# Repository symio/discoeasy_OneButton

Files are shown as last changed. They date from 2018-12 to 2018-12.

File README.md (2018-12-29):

# discoeasy_OneButton
Modifications pour Marlin_1.1.0RC6 par Dagoma afin d'activer la prise en compte d'un bouton pause/marche sur l'entrée Z-

Ce mod permet également de conserver certains réglages en vue de futures mises à jour.

vous pouvez configurer : 

 - Le nom de votre imprimante 
 - Le nivelage à 9 points de palpage (non proposé par Dagoma) 
 - Le bouton pause sans dépendance de l'extrudeur+ 
 - L'inversion des ports des extrudeurs
 - Les trapézoïdales sans pack expert 
 - Les pid x,y,z et E 

# Disclaimer :
Je ne suis pas associé ni employé par la société Dagoma.
Ce que je vous propose ici fonctionne sur ma DiscoEasy 200 équipée d'un écran et sur la base du firmware officiel Dagoma à partir du date du 2018/04/04-14h27 
choisit sur https://dist.dagoma.fr/ avec pour options : "avec écran" et "sans filamentRunout".

Ce mod est compatible avec le pack expert ou un pack expert maison ainsi qu'avec l'extrudeur +.

L'objectif et d'activer le mode de changement rapide de filament sur l'action d'un bouton comme Dagoma le propose dans son AddOn numéro2 "extrudeur+" sans l'extrudeur amélioré par Dagoma.
Pour fonctionner vous devez connecter un bouton poussoir sur le port "z-" de la carte MKS base.

L'objectif secondaire est de conserver vos personnalisation du firmware en cas de mise à jour.

N'hésitez pas à me contacter pour demander des ajouts de config.

C'est ce mod que j'utilise sur mon imprimante et pour moi cela fonctionne. 
Je suis prêt à vous aider mais n'endosserais aucune responsabilité quand à l'usage de ce mod.
Je considère que je m'adresse à des adultes responsables prêt à prendre à leurs charge leurs responsabilités.

Vous utilisez ce hack à vos risques et périls.

# configuration :

Lisez ce [guide](https://github.com/symio/discoeasy_OneButton/blob/master/config.md) pour configurer vos options.

Tous les détails de configuration et explications s'y trouvent.

# installation :

 - Copiez les fichiers dans le répertoire Marlin ou vous avez extrait les derniers fichiers source fournit par Dagoma (cf https://dist.dagoma.fr/)
Pour installer ce hack vous avez 2 possibilités :
1°) appliquer des patchs
 - Appliquez les patchs de code source fournit sur ce dépôt :
 -- Configuration.h.patch
 -- pins.h.patch
 -- ultralcd.cpp.patch
 
 2°) Modifiez les fichiers de code sources suivants :
- Configuration.h :
 Ligne 41  ajoutez :

```cpp
 #define MODED_EASY_BOARD
```
- Fichier pins.h à la fin du fichier ajoutez :

```cpp
#if defined(MODED_EASY_BOARD) && !defined(MODED_EASY_H)
  #include "moded_easy.h"
#endif
```
- Fichier ultralcd.cpp remplacez la ligne 762 telle que :

```cpp
    //#if ENABLED(SUMMON_PRINT_PAUSE)
    #if ENABLED(SUMMON_PRINT_PAUSE) && ENABLED(FILAMENT_RUNOUT_SENSOR)
```
# Appliquer les fichiers de patchs :
1°) sous Linux :
- Ouvrez un terminal et naviguer jusqu'à vos sources
`$ cd ~/Documents/Marlin/`
- Vérifiez la présence des patchs :
```
$ ll *.patch
 Configuration.h.patch
 pins.h.patch
 ultralcd.cpp.patch
```
- Patchez chaque fichier individuellement :
`$ patch Configuration.h < Configuration.h.patch`
`$ patch pins.h < pins.h.patch`
`$ patch ultralcd.cpp < ultralcd.cpp.patch`

2°) sous Windows :
- Suivez cette documentation : https://docs.moodle.org/dev/How_to_apply_a_patch
- placez votre terminal au répertoire sources fourni par Dagoma (et dans lequel vous avez copié les fichiers de patch et la configuration)
- Patchez chaque fichier individuellement :
`c:\bin\patch.exe Configuration.h < Configuration.h.patch`
`c:\bin\patch.exe pins.h < pins.h.patch`
`c:\bin\patch.exe ultralcd.cpp < ultralcd.cpp.patch`

# Options de configuration :
Dans le fichier moded_easy.h :
- Les lignes 3 et 5 permettent de choisir :
-- ligne 3 Auto nivellage à 9 points avec bonne couverture de la surface du plateau
-- ligne 5 Mod one button
- commentez ou décommentez les lignes qui vous interressent
-- ex: activer le mod : (ligne 5)
`  #define ONE_BUTTON_MOD	 // active ou désactive le mod one button`
-- ex: désactiver le mod : (ligne 5)
`  //#define ONE_BUTTON_MOD	 // active ou désactive le mod one button`

# compiler et flasher l'imprimante

En suivant les tutos disponibles sur internet (https://www.lesimprimantes3d.fr/forum/topic/6228-tuto-flasher-firmware-discoeasy/) compilez et téléverser votre firmaware modifié avec Arduino dans votre imprimante.

# conclusion :
Il ne vous reste qu'à brancher un bouton poussoir sur le endstop Z- comme sur la vidéo de montage de l'extrudeur+ sur le site de Dagoma.

Enjoy et n'hésitez pas à envoyer des pull requests ou ouvrir des tickets si vous avez des soucis.

Photos et vidéo du montage ici : https://www.lesimprimantes3d.fr/forum/topic/14344-mod-bouton-pausechange-fil-pour-discoeasy200/

Le stl de face avant modifiée est là : https://www.tinkercad.com/things/0Ngym5hLYUM-discoeasy200modonebutton

Merci au Dagonautes sur le forum et sur Facebook vous êtes géniaux les mecs (et les filles) (sauf un ou deux dont moi bien sur) ...

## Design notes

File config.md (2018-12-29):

# Loamok ModedEasy200 configuration

Allez hop nouvelle version vous pouvez configurer : 

 - Le nom de votre imprimante 
 - Le nivelage à 9 points de palpage (non proposé par Dagoma) 
 - Le bouton pause sans dépendance de l'extrudeur+ 
 - L'inversion des ports des extrudeurs
 - Les trapézoïdales sans pack expert 
 - Les pid x,y,z et E (en très haute précision)
 
## Le nom de l'imprimante :
Dé-commentez la ligne 3 et changez (si vous le voulez) le nom ici je vous propose "ModedEasy200" :

    #define MODED_MACHINE_NAME "ModedEasy200"

## leveling en 9 points
Dé-commentez la ligne 4 pour activer le leveling en 9 points (plus précis que les 5 points de Dagoma) :

    #define MOD_BED_LEVELING_9P

## Le bouton pause sans dépendance de l'extrudeur+
Dé-commentez la ligne 6 pour activer le bouton pause non dépendant du détecteur de filament :

    #define ONE_BUTTON_MOD

## Inversion des ports extrudeurs
Vous pouvez inverser les ports d'extrudeurs (E1 en E0 et vice et versa) en dé-commentant la ligne 7

    #define MODED_INVERT_EXTRUD

## Les trapézoïdales avec ou sans pack expert 
Vous pouvez définir votre imprimante comme utilisant des tiges trapézoïdales sans pack expert en dé-commentant la ligne 8 
(configurez aussi les pid en dessous à 80, 80, 400, 98 pour les trapez)

    #define MODED_TRAPEZ

## Les pid x,y,z et E 
Vous pouvez définir les pid de votre imprimante en dé-commentant la ligne 9 et en les configurant lignes 13 à 17 

    #define MODED_PRECISION
    #define MODED_PID_X 80 // X Par défaut la valeur dagoma est 80
    #define MODED_PID_Y 80 // Y Par défaut la valeur dagoma est 80
    #define MODED_PID_Z 2560// Z Par défaut la valeur dagoma est 400 
    #define MODED_PID_E 98  // E pour extrudeur
Les valeurs sont :

 - X Dagoma : 80 ; X chez moi : 79.4934
 - Y Dagoma : 80 ; Y chez moi : 79.2864
 - Z Dagoma filetés : 2560 ; Z Dagoma Trapez (pack expert) : 400  ; Y chez moi : 397.2195
 - E Dagoma : 98 ; E chez moi : 100.8023
Reportez vous à cette discussion pour bien régler vos pid :
https://www.lesimprimantes3d.fr/forum/topic/3394-tuto-calcul-des-steps-per-mmunit-une-fois-pour-toutes/

Il est possible d'utiliser directement vos mesures pour réaliser la config des steps per millimeter.

Pour ce faire :

En configuration de base Dagoma : (80, 80, 2560 ou 400, 98) imprimez une pièce de réglage.

Je vous joint un fichier stl un peu plus grand qu'un cube de réglage car je trouve plus pertinent d'utiliser une plus grande taille de mesure cela donne une meilleure précision.

Vous l'imprimez en standard (0.2, avec amélioration d'adhérence (bordure pas radeau qui peux fausser la hauteur) avec le slicer de votre choix.

Vous mesurez la taille de la pièce imprimée qui est censé faire 100*100*100

Vous reportez la taille mesurée dans les calculs de la configuration tels que (par exemple après impression mes mesures étais (100.18Y, 99.69X, 100.14Z) :)

```
  // ceci est un exemple ne réécrivez pas ça tel quel svp
  // #define MODED_PID_[xyz] (<spmOriginel>*(100/<mesure>))
    #define MODED_PID_X (80*(100/100.18))
    #define MODED_PID_Y (80*(100/99.69))
    #define MODED_PID_Z (400*(100/100.14)) // #define MODED_PID_Z (2560*(100/100.14)) pour des tiges filetées
```
Vous activez bien le mod_precision en décommentant la ligne 9 et enregistrez

  #define MODED_PRECISION

Vous téléversez le firmware, et redémarrez l'imprimante.

Vous repérez votre réglage de z-offset.

Vous "réinitialisez" les réglages d'usine ou par défaut et refaites votre z-offset.

Réimprimez la pièce de réglages et vérifiez que les mesures vous conviennent.

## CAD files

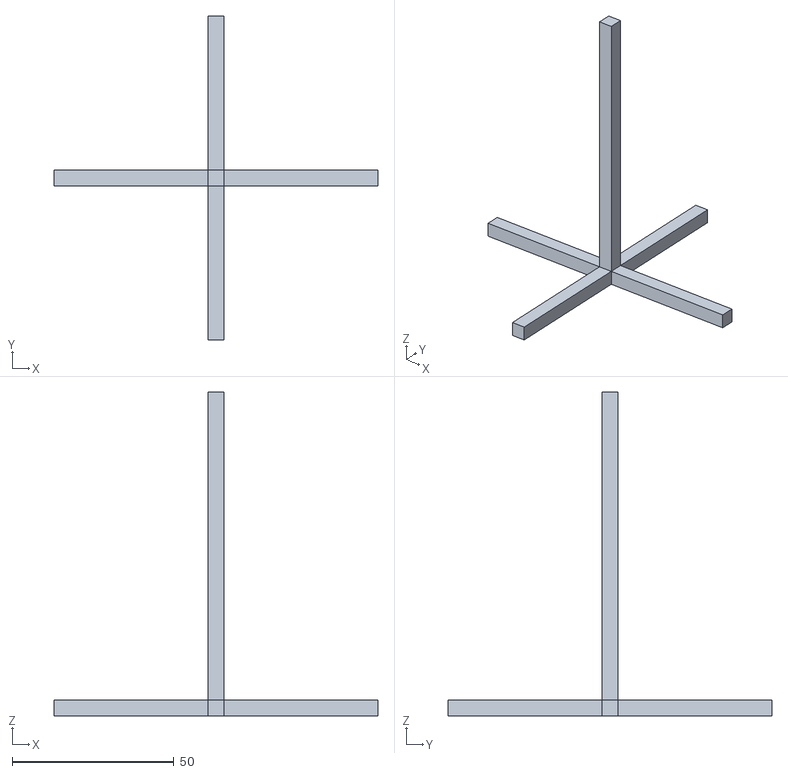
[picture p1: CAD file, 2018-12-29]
reglagePrecision.stl
100.0 x 100.0 x 100.0

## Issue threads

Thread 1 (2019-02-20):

Patch ultralcd

dagorel, 2019-02-20:
Bonjour @symio ,

J'ai bien noté ton commentaire concernant la pause sans detect-fil. J'essaierai de l'intégrer pour la prochaine version. J'ai créé une issue sur le repo github du Marlin Dagoma:
https://github.com/dagoma3d/Marlin-By-Dagoma/issues/13

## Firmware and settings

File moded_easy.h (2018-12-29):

#ifndef MODED_EASY_H
    #define MODED_EASY_H// Mettez le nom de machine entre '"'
    #define MODED_MACHINE_NAME "ModedEasy200" // Décommentez pour changer le nom de la machine
//    #define MOD_BED_LEVELING_9P // décommentez (enlevez les "//" en début de ligne) pour 
				 // activer le leveling en 9 points
    #define ONE_BUTTON_MOD	 // active ou désactive le mod one button (fonctionne avec le pack extru+)
//    #define MODED_INVERT_EXTRUD // invertion extrudeur 0 en extrudeur 1
//    #define MODED_TRAPEZ        // Z en trapézoïdales avec ou sans pack expert
//    #define MODED_PRECISION     // Définition de la précision des prints 
                                // (très utile pour personaliser les pid)
//  Et définissez vos pid (steps per millimeter) ci-dessous voir :
//  https://www.lesimprimantes3d.fr/forum/topic/3394-tuto-calcul-des-steps-per-mmunit-une-fois-pour-toutes/
    #define MODED_PID_X 80      // X Par défaut la valeur dagoma est 80
    #define MODED_PID_Y 80      // Y Par défaut la valeur dagoma est 80
    #define MODED_PID_Z 2560    // Z Par défaut la valeur dagoma est 400 
                                // en trapez pack expert et 2560 en filetés standard 
    #define MODED_PID_E 98      // E (extru) Par défaut la valeur dagoma est 98
//  Vous pouvez utiliser directement des caculs d'adaptation des stepsPerMillimeter :
// ceci est un exemple ne réécrivez pas ça tel quel svp
//    #define MODED_PID_[xyz] (<spmOriginel>*(100/<mesure>))
//    #define MODED_PID_X (80*(100/100.18))
//    #define MODED_PID_Y (80*(100/99.69))
//    #define MODED_PID_Z (400*(100/100.14)) // #define MODED_PID_Z (2560*(100/100.14)) pour des tiges filetées
#endif
/*-----------------------------------------------------------------------------*/
// Fin de config ne touchez à rien ci-dessous configurez ce que vous voulez au dessus de cette ligne
/*-----------------------------------------------------------------------------*/
#ifdef MODED_EASY_BOARD
  // Configuration.h
  #ifdef MODED_MACHINE_NAME
    #undef CUSTOM_MACHINE_NAME
    #define CUSTOM_MACHINE_NAME MODED_MACHINE_NAME
  #endif
  #ifdef MOD_BED_LEVELING_9P
  // palpage en 9 points avec meilleure prise en compte de la taille du plateau
    #undef LEFT_PROBE_BED_POSITION
    #define LEFT_PROBE_BED_POSITION 2
    #undef RIGHT_PROBE_BED_POSITION
    #define RIGHT_PROBE_BED_POSITION 200
    #undef FRONT_PROBE_BED_POSITION
    #define FRONT_PROBE_BED_POSITION 25
    #undef BACK_PROBE_BED_POSITION
    #define BACK_PROBE_BED_POSITION 205
    #undef AUTO_BED_LEVELING_GRID_POINTS
    #define AUTO_BED_LEVELING_GRID_POINTS 3
  #endif

  #if defined(ONE_BUTTON_MOD) && !ENABLED(FILAMENT_RUNOUT_SENSOR) && !defined(ONE_BUTTON)
  // one button mod
    #define ONE_BUTTON_INVERTING true
    #define ONE_BUTTON
    #define SUMMON_PRINT_PAUSE_SCRIPT "M600 U5 V195 X195 Y195"
    #define SUMMON_PRINT_PAUSE_INVERTING true
    #define SUMMON_PRINT_PAUSE

  // pins.h
    #undef SUMMON_PRINT_PAUSE_PIN
    #define SUMMON_PRINT_PAUSE_PIN 18
    #undef ONE_BUTTON_PIN
    #define ONE_BUTTON_PIN SUMMON_PRINT_PAUSE_PIN
  #endif
  #ifdef MODED_INVERT_EXTRUD
  // invertion du port extrudeur (si vous n'avez pas modifié le branchement de votre 
  // extrudeur commentez la ligne 4)
  // pins_RAMPS_14.h
    #undef E1_STEP_PIN
    #define E1_STEP_PIN        26
    #undef E1_DIR_PIN
    #define E1_DIR_PIN         28
    #undef E1_ENABLE_PIN
    #define E1_ENABLE_PIN      24

    #undef E0_STEP_PIN
    #define E0_STEP_PIN        36
    #undef E0_DIR_PIN
    #define E0_DIR_PIN         34
    #undef E0_ENABLE_PIN
    #define E0_ENABLE_PIN      30
  #endif
  #ifdef MODED_TRAPEZ
    #undef DEFAULT_AXIS_STEPS_PER_UNIT
    #ifdef MODED_PRECISION
      #define DEFAULT_AXIS_STEPS_PER_UNIT {MODED_PID_X, MODED_PID_Y, MODED_PID_Z, MODED_PID_E}
    #else
      #define DEFAULT_AXIS_STEPS_PER_UNIT {80, 80, 400, 98}
    #endif
  #else
    #ifdef MODED_PRECISION
      #undef DEFAULT_AXIS_STEPS_PER_UNIT
      #define DEFAULT_AXIS_STEPS_PER_UNIT {MODED_PID_X, MODED_PID_Y, MODED_PID_Z, MODED_PID_E}
    #endif
  #endif
#endif

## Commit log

2018-04-08 Ajout dans la doc
2018-04-08 Modif dans la doc
2018-04-08 Url de publication
2018-04-08 Url de publication redesign face avant
2018-12-15 Mise à jour suite à sortie du pack bicolore et mise à jour par dagoma Ajout de config possible et correction d'un bug probable
    [moded_easy.h]
2018-12-15 Ajout du lien vers le guide de configuration
2018-12-15 Problème de relecture
2018-12-29 Mise à jour doc et prise en compte calcul des spmu
    [reglagePrecision.stl]
